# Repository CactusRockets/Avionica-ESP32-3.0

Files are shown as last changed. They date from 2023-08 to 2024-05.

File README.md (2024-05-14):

# Placas da aviônica para o foguete Turing-500m

Nesse repositório temos os arquivos das placas que farão parte da aviônica do foguete Turing de 500m da Cactus Rockets Design.

### Descrição

Temos duas placas principais para esta aviônica:
- Placa de Processamento
- Placa de Acionamento

A placa de processamento é responsável pelo processamento dos dados dos módulos, armazenamento desses dados e telemetria. A placa de acionamento possui o circuito necessário para a correta ativação do Skib.

OBS.: Os arquivos das placas podems ser abertos por meio software Eagle da Autodesk.

### Esquemáticos e layouts

### Conexões entre placas

### Funcionamento

A placa de processamento contém um switch de ativação do sistema. No momento que o switch é pressionado, o sistema liga e faz a leitura dos módulos. Após cada leitura, ele armazena esses valores no microSD e envia esses dados via telemetria.

No momento que a placa de processamento detectar uma queda, ela envia um sinal para a placa de acionamento para que a mesma ative o Skib da parte de recuperação.

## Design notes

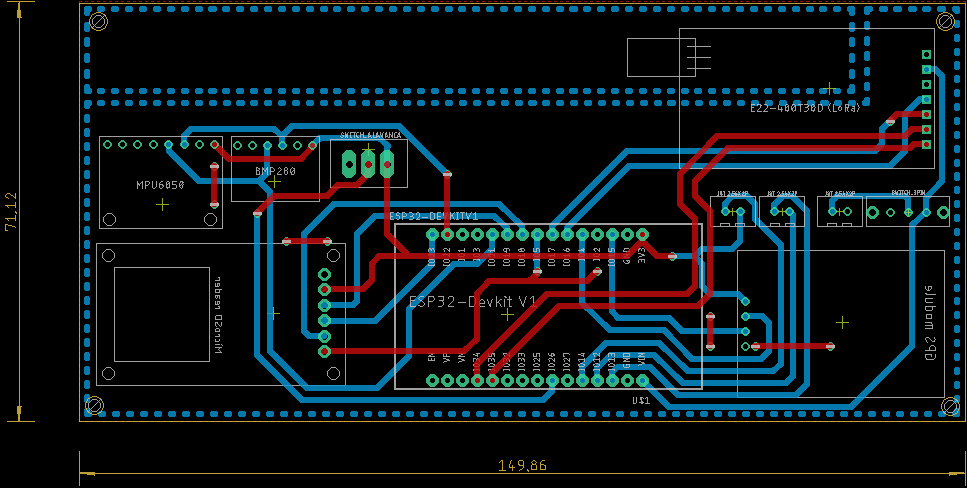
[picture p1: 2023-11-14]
Placa de processamento/500m/PCB - 500m.png

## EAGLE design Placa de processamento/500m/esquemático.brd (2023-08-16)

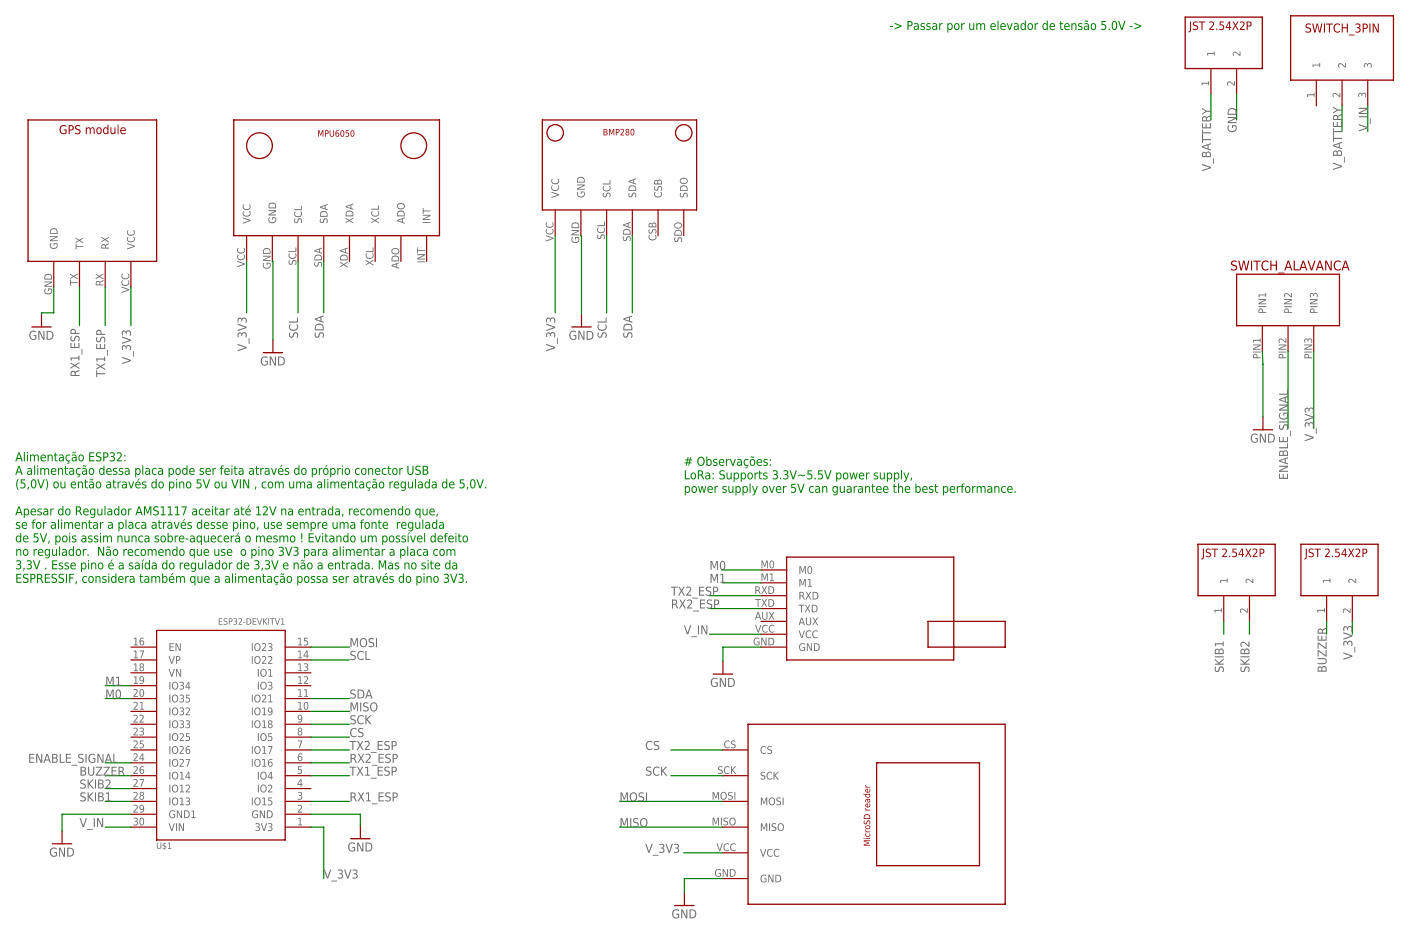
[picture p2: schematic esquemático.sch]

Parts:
U$1: ESP32DEVKITV1; ESP32-DEVKITV1
U$2: E22-400T30D; E22-400T30D_FOOTPRINT
U$3: GPS_MODULE; GPS_MODULE_FOOTPRINT
U$4: BMP280V1; BMP280_FOOTPRINT
U$5: SWITCH_ALAVANCA; SWITCH_ALAVANCA_FOOTPRINT
U$6: MPU6050V1; MPU6050_FOOTPRINT
U$7: MICROSD_READER; MICROSD_READER_FOOTPRINT
U$8, U$9, U$12: JST2.54X2P; JST2.54X2P_FOOTPRINT
U$11: SWITCH_3PIN

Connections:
BUZZER: U$1.26 (IO14), U$9.1
CS: U$1.8 (IO5), U$7.CS
ENABLE_SIGNAL: U$1.24 (IO27), U$5.PIN2
GND: U$1.2 (GND), U$1.29 (GND1), U$2.GND, U$3.GND, U$4.GND, U$5.PIN1, U$6.GND, U$7.GND, U$12.2
M0: U$1.20 (IO35), U$2.M0
M1: U$1.19 (IO34), U$2.M1
MISO: U$1.10 (IO19), U$7.MISO
MOSI: U$1.15 (IO23), U$7.MOSI
RX1_ESP: U$1.3 (IO15), U$3.TX
RX2_ESP: U$1.6 (IO16), U$2.TXD
SCK: U$1.9 (IO18), U$7.SCK
SCL: U$1.14 (IO22), U$4.SCL, U$6.SCL
SDA: U$1.11 (IO21), U$4.SDA, U$6.SDA
SKIB1: U$1.28 (IO13), U$8.1
SKIB2: U$1.27 (IO12), U$8.2
TX1_ESP: U$1.5 (IO4), U$3.RX
TX2_ESP: U$1.7 (IO17), U$2.RXD
V_3V3: U$1.1 (3V3), U$3.VCC, U$4.VCC, U$5.PIN3, U$6.VCC, U$7.VCC, U$9.2
V_BATTERY: U$11.2, U$12.1
V_IN: U$1.30 (VIN), U$2.VCC, U$11.3

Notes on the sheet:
-> Passar por um elevador de tensão 5.0V ->
# Observações: LoRa: Supports 3.3V~5.5V power supply, power supply over 5V can guarantee the best performance.
Alimentação ESP32: A alimentação dessa placa pode ser feita através do próprio conector USB (5,0V) ou então através do pino 5V ou VIN , com uma alimentação regulada de 5,0V. Apesar do Regulador AMS1117 aceitar até 12V na entrada, recomendo que, se for alimentar a placa através desse pino, use sempr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

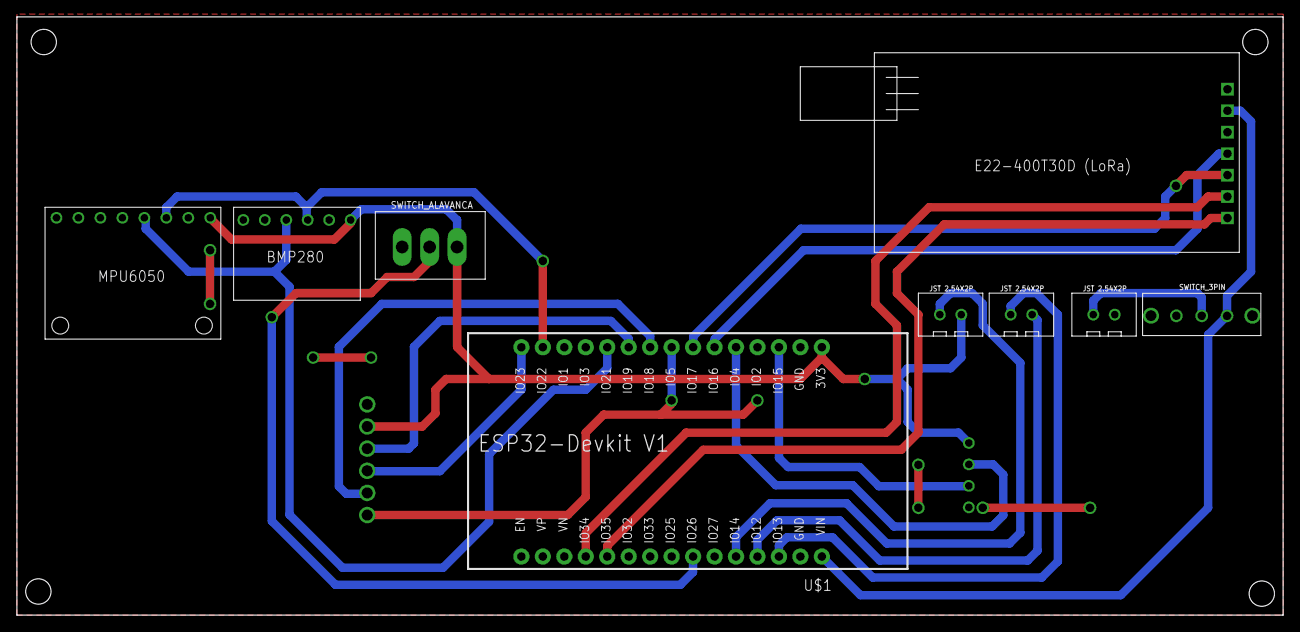
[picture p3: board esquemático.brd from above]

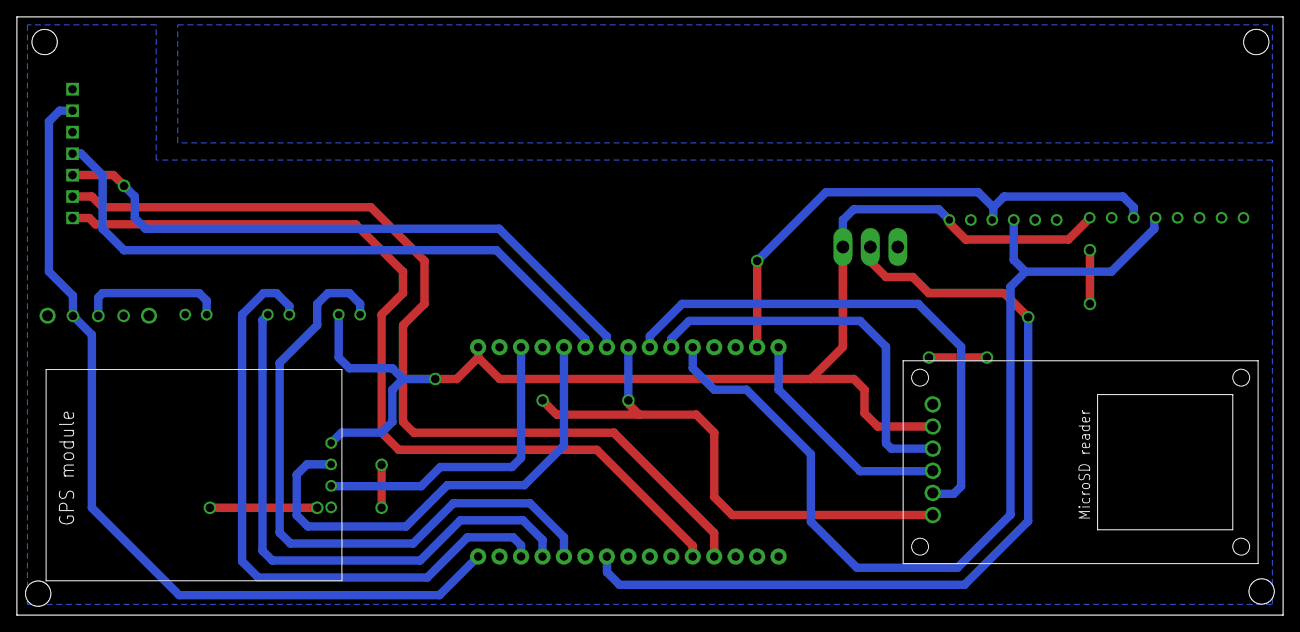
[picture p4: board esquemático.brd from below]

Board: 2 copper layers, 149.8 x 70.8 mm, 11 parts (2 on the bottom side), 20 nets.

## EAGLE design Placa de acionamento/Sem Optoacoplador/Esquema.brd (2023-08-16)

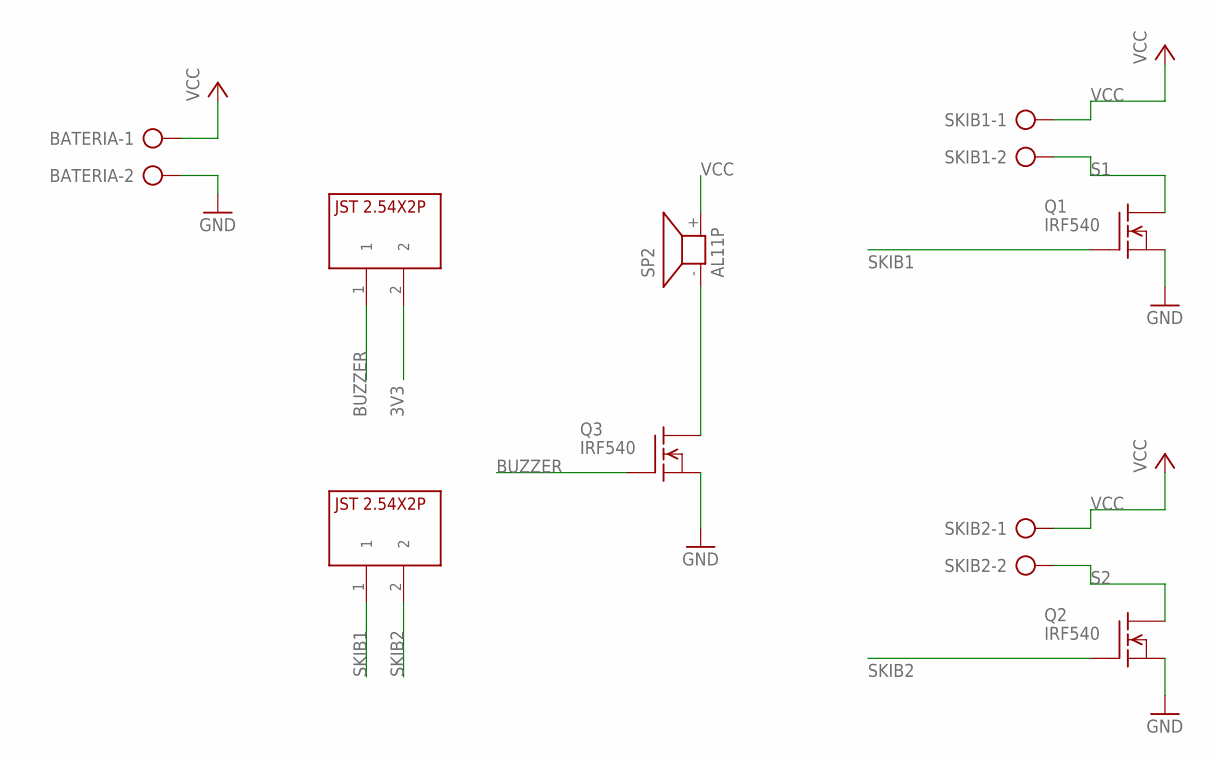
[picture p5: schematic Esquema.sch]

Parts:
BATERIA: AK500/2-H
Q1, Q2, Q3: IRF540; TO220
SKIB1, SKIB2: AK500/2-H
SP2: AL11P
U$1, U$2: JST2.54X2P; JST2.54X2P_FOOTPRINT

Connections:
3V3: U$1.2
BUZZER: Q3.1 (G), U$1.1
GND: BATERIA.2, Q1.3 (S), Q2.3 (S), Q3.3 (S)
unnamed: Q3.2 (D), SP2.- (1)
S1: Q1.2 (D), SKIB1.2
S2: Q2.2 (D), SKIB2.2
SKIB1: Q1.1 (G), U$2.1
SKIB2: Q2.1 (G), U$2.2
VCC: BATERIA.1, SKIB1.1, SKIB2.1, SP2.+ (2)

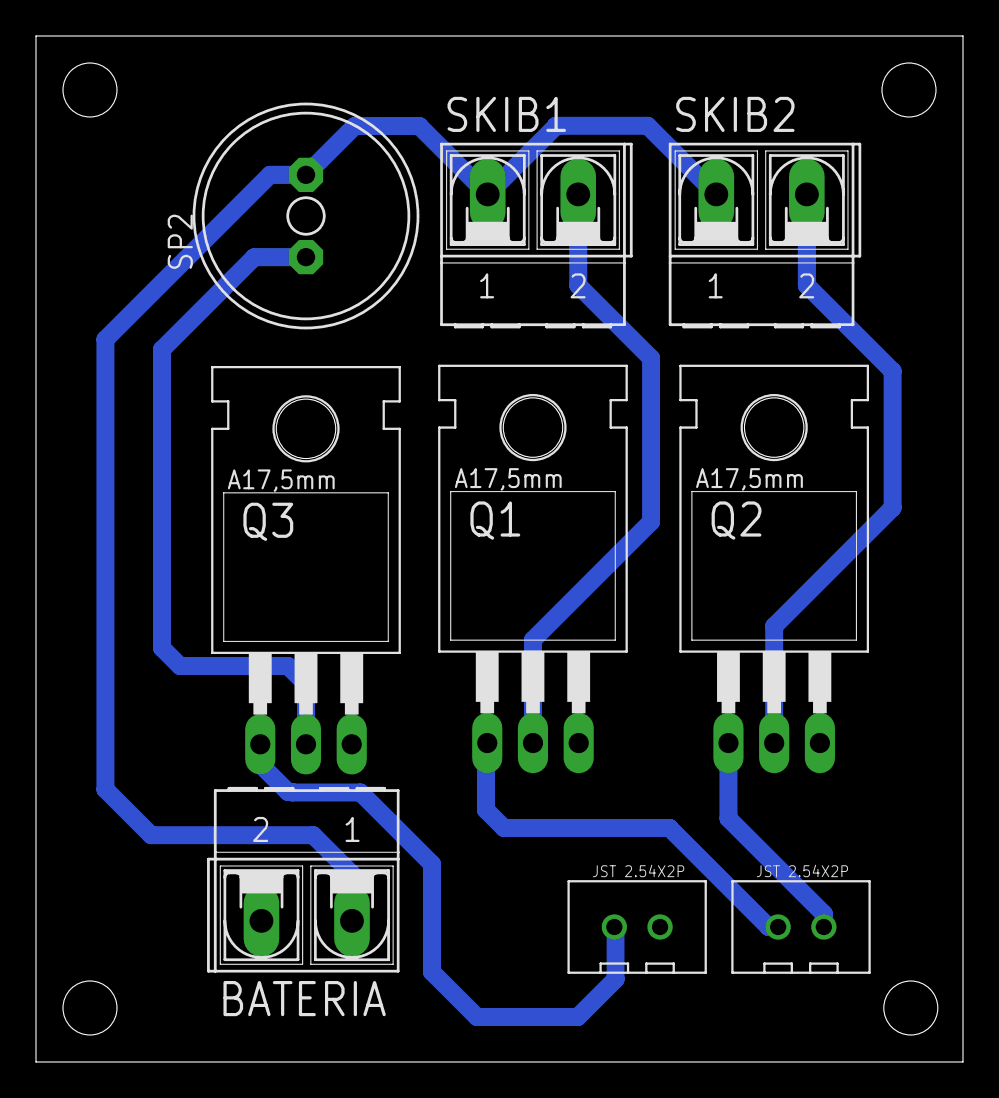
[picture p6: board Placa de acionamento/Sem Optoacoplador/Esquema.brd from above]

Board: 2 copper layers, 51.5 x 57.0 mm, 9 parts (0 on the bottom side), 8 nets.

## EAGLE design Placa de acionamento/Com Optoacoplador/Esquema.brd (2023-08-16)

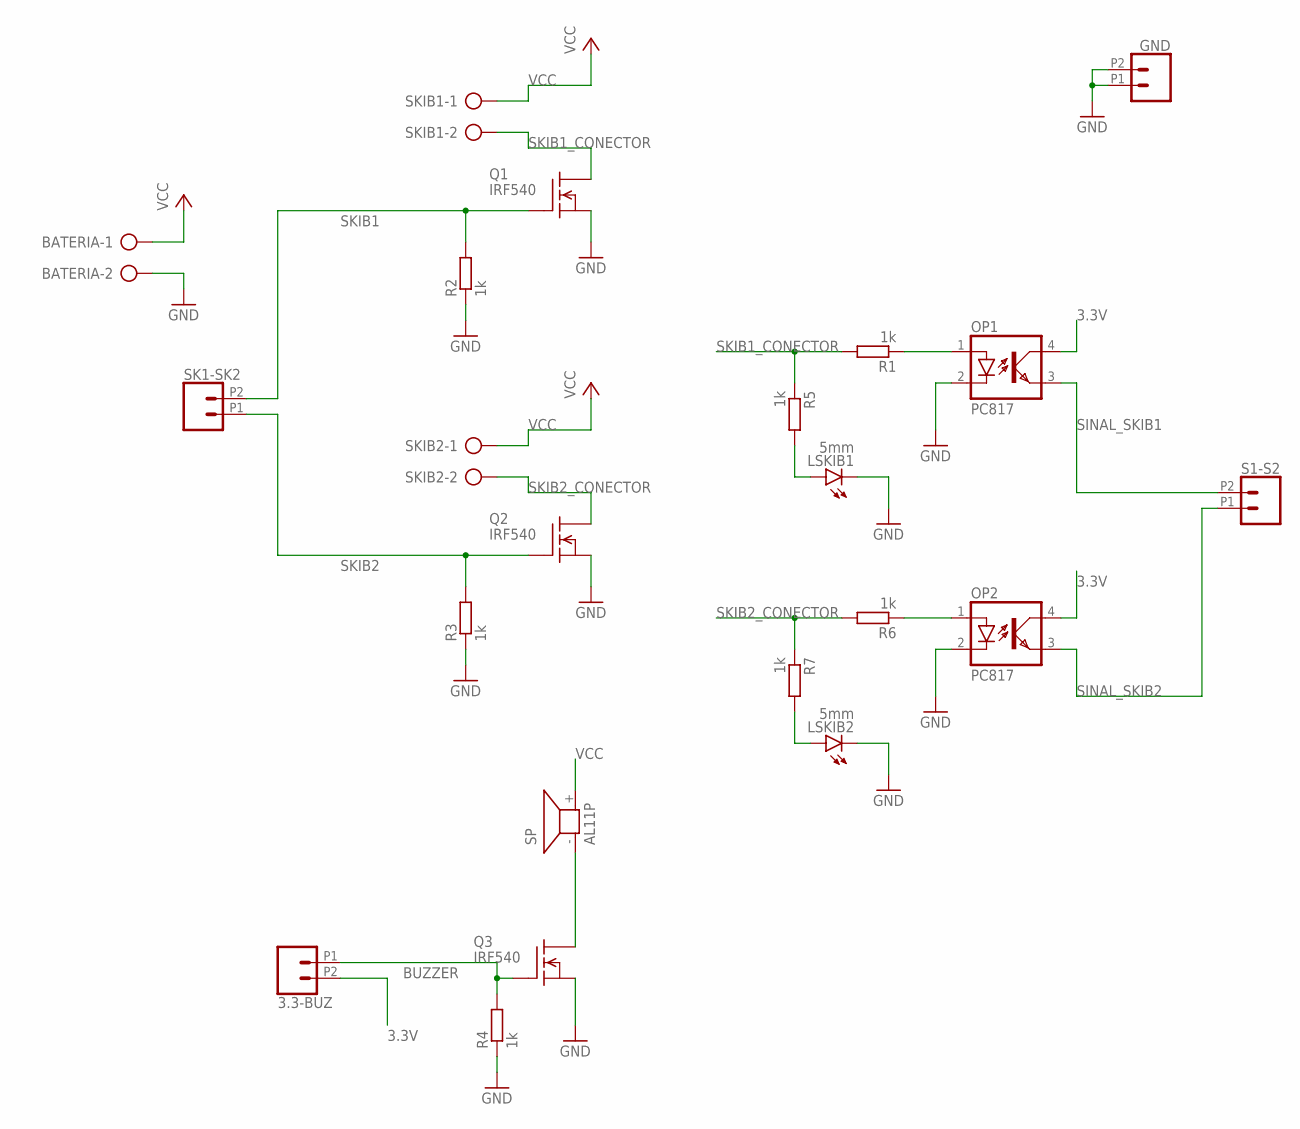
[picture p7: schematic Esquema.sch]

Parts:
3.3-BUZ: CONN_022.54MM_SCREWTERM; 1X02_2.54_SCREWTERM
BATERIA: AK500/2-H
GND: CONN_022.54MM_SCREWTERM; 1X02_2.54_SCREWTERM
LSKIB1, LSKIB2: 5mm; LED5MM
OP1, OP2: PC817; DIL04
Q1, Q2, Q3: IRF540; TO220
R1, R2, R3, R4, R5, R6, R7: 1k; 0207/10
S1-S2: CONN_022.54MM_SCREWTERM; 1X02_2.54_SCREWTERM
SK1-SK2: CONN_022.54MM_SCREWTERM; 1X02_2.54_SCREWTERM
SKIB1, SKIB2: AK500/2-H
SP: AL11P

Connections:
3.3V: 3.3-BUZ.P2 (2), OP1.4 (COL), OP2.4 (COL)
BUZZER: 3.3-BUZ.P1 (1), Q3.1 (G), R4.2
GND: BATERIA.2, GND.P1 (1), GND.P2 (2), LSKIB1.K (C), LSKIB2.K (C), OP1.2 (C), OP2.2 (C), Q1.3 (S), Q2.3 (S), Q3.3 (S), R2.1, R3.1, R4.1
unnamed: LSKIB2.A, R7.2
unnamed: Q3.2 (D), SP.- (1)
unnamed: LSKIB1.A, R5.2
unnamed: OP1.1 (A), R1.1
unnamed: OP2.1 (A), R6.1
SINAL_SKIB1: OP1.3 (EMIT), S1-S2.P2 (2)
SINAL_SKIB2: OP2.3 (EMIT), S1-S2.P1 (1)
SKIB1: Q1.1 (G), R2.2, SK1-SK2.P2 (2)
SKIB1_CONECTOR: Q1.2 (D), R1.2, R5.1, SKIB1.2
SKIB2: Q2.1 (G), R3.2, SK1-SK2.P1 (1)
SKIB2_CONECTOR: Q2.2 (D), R6.2, R7.1, SKIB2.2
VCC: BATERIA.1, SKIB1.1, SKIB2.1, SP.+ (2)

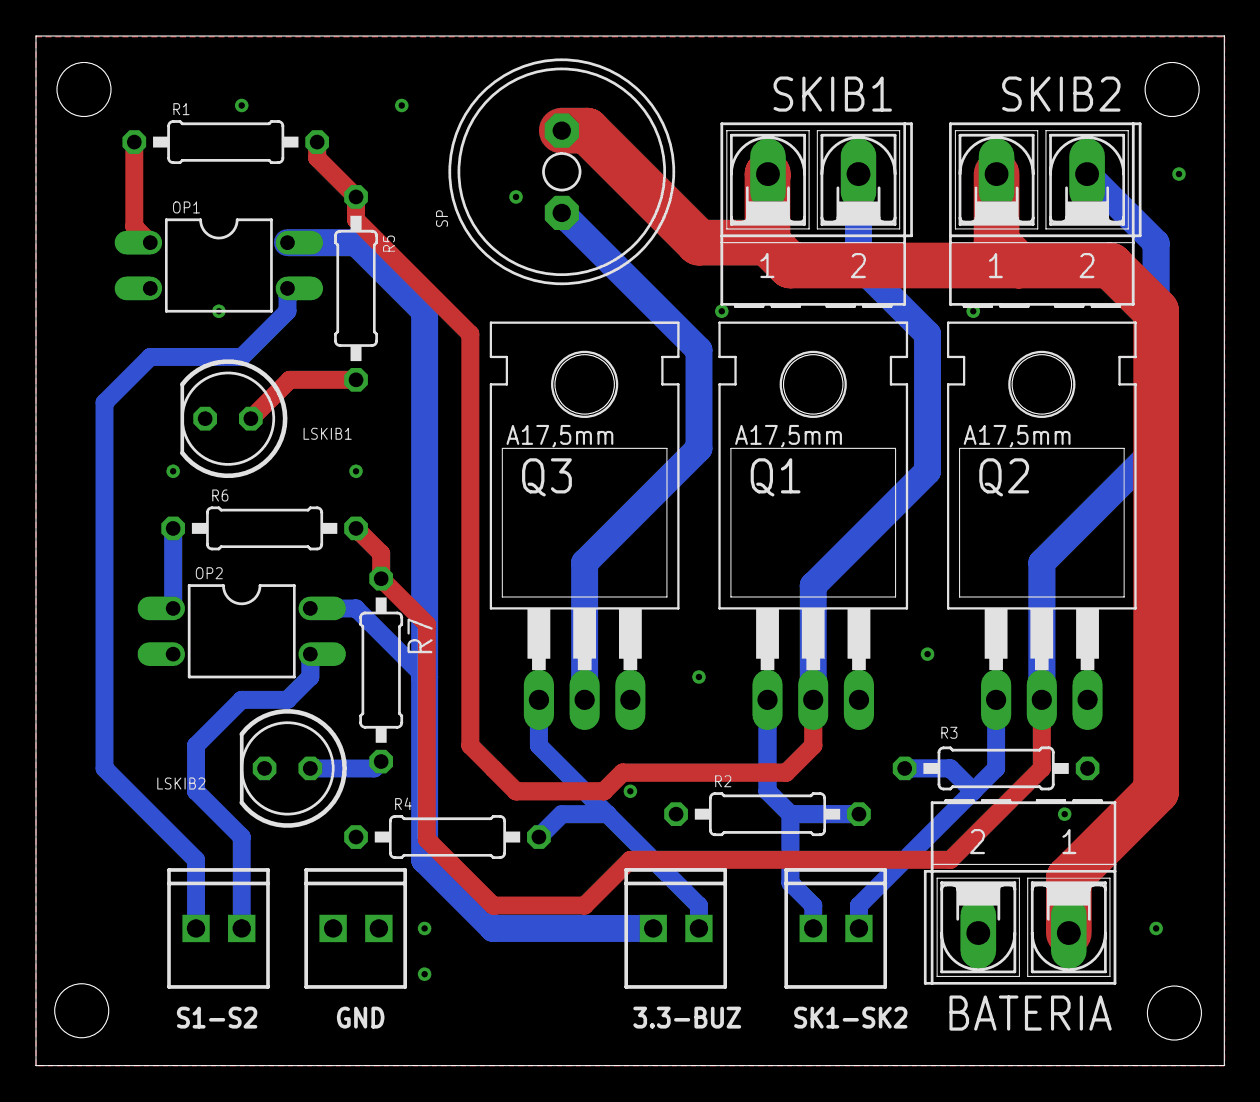
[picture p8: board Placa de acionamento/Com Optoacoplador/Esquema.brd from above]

Board: 2 copper layers, 66.0 x 57.2 mm, 22 parts (0 on the bottom side), 15 nets.

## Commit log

2023-07-31 Update paraquedas
    [Esquema.brd, Esquema.sch]
2023-08-01 Atualização-avionica
    [Avionicapart1.brd, Avionicapart1.sch, MODULO GPS.brd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]
2023-08-01 atualização Avionica
    [Avionicapart1.brd]
2023-08-01 correções avionica e paraquedas
    [Avionicapart1.brd, Avionicapart1.sch, Esquema.brd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]
2023-08-10 Atualização de trilhas
    [Avionicapart1.brd, Avionicapart1.sch, Esquema.brd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]
2024-04-16 Create Esquema 2 mosfets

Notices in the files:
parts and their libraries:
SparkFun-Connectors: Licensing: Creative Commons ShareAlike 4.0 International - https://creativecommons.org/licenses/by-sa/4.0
